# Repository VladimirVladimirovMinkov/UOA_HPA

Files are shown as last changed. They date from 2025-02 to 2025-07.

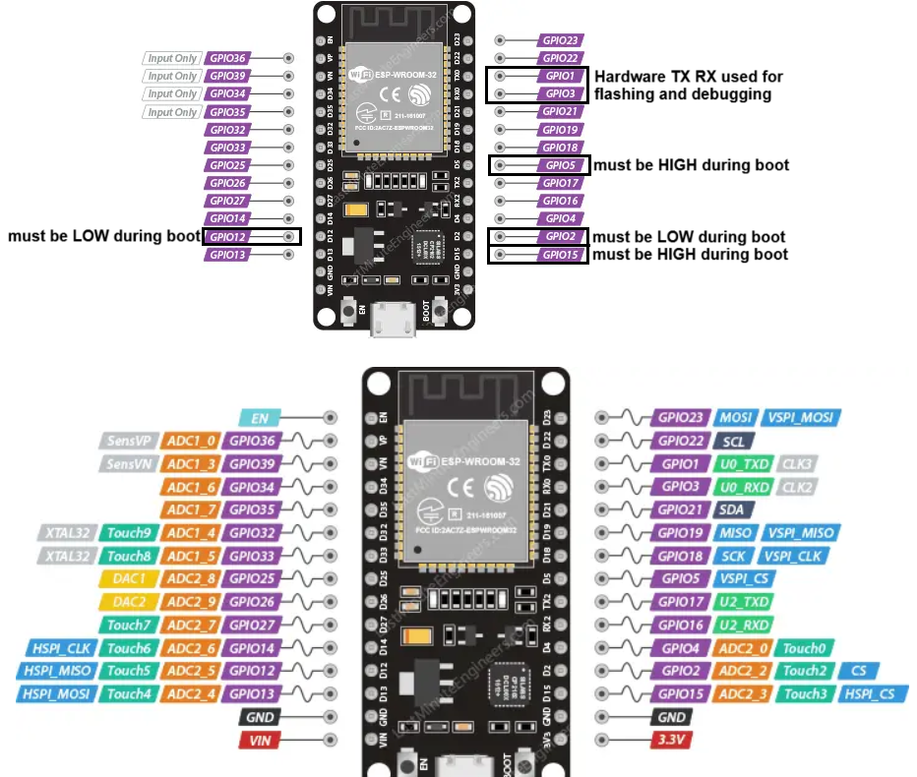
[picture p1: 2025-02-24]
src/ESP32 test code 1/esp32 wroom32 workable pins.png

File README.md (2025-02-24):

# UACHPA

This is a code and document repository for the University of auckland Aeronaughtics Club Human Powered Aircraft

# Overview

Repository Structure:
* Documents: This folder contains documents and reports made relating to the HPA
* CAD: Contains Computer Aided Design projects such as SOLIDWORKS or KiCAD
* src: This is for the code for the control systems and input mapping
* Test: This is the RnD folder for prototypes and demos that don't 100% work

# Getting involved
Please respect the repository structure and make sub folders if you're adding to the project so it is easier to navigate the repository

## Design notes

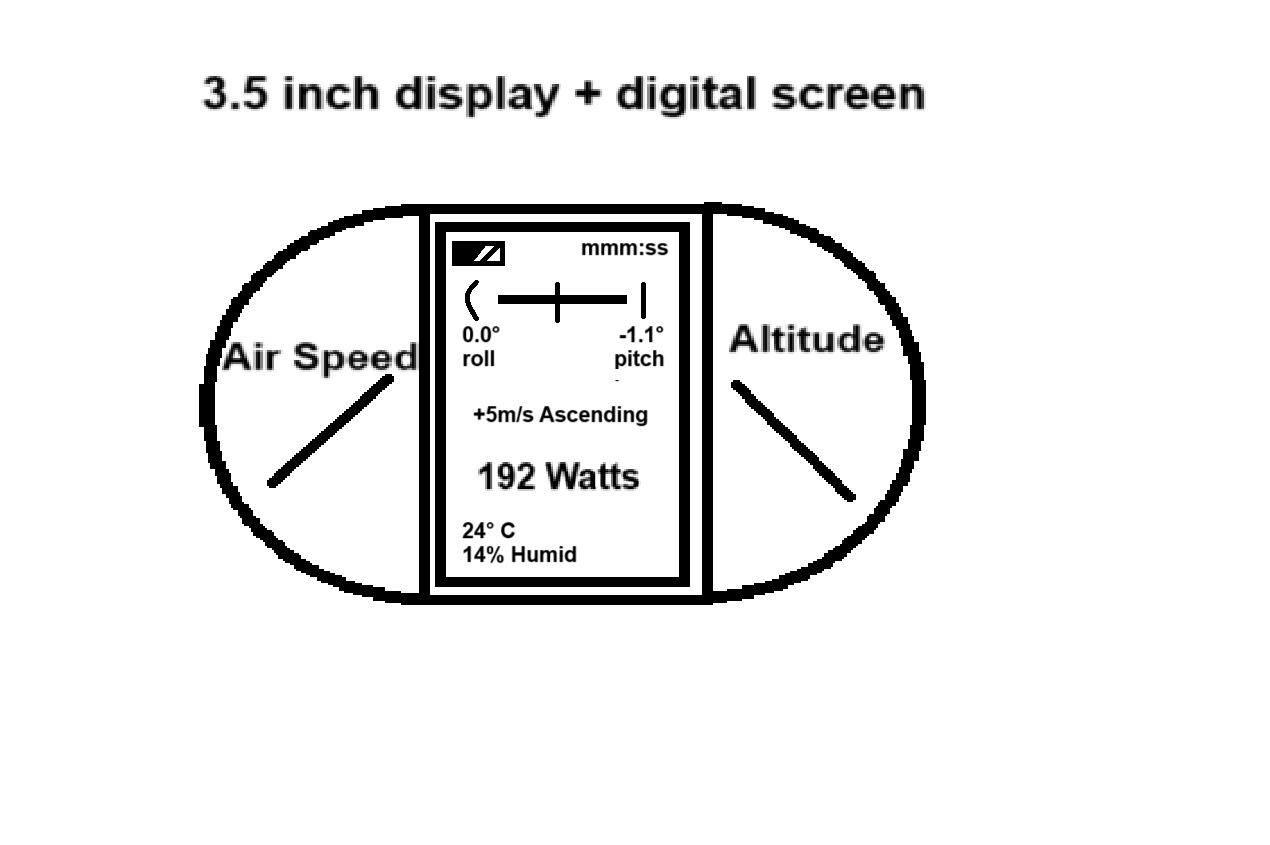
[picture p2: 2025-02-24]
Documents/Made/new display.png

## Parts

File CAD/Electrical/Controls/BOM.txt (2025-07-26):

'Value' 'Qty'
'4.7uf Capacitor' '4'
'10uf Capacitor' '5'
'Servo' '2'
'SD card reader' '1'
'BME280' '1' or BMP just don't get the connections confused
'potentiometer' '2'
'Battery 3.6V' '6' minimum we want 2
'Restart/Boot Button' '1'
'GPS' '1'
'Cadence Sensor Hall Effect' '4'
'Gyroscope' '1'
'LCD' '1'
'pitot tube assembly' '1'
'0ohm Jumper' '3' wire or 0ohm resistor or solder connection
'10k resistor' '4'
'1k resistor' '3'
'12k resistor' '1'
'23.3k resistor' '1'
'3.5k resistor' '1'
'5V regulator' '1'
'3V3 regulator' '1'
'3-6V to 6V DC/DC converter' '1'
'ESP32-WROOM-32E' '1'

'SD card Connector' '1' 1x6
'External Connector' '1' 1x4
'BME280 Connector' '1' 1x4
'Pitch Control Connector' '1' 1x3
'Roll Control Connector' '1' 1x3
'SD card selecting jumper' '1' 1x15
'SD card selecting connector' '1' 1x4
'Battery Connector' '1' 1x4 we can use a 1x2 if we don't use a charger and make our own battery pack
'GPS Connector' '1' 1x4
'Cadence Sensor Connector' '4' 1x3
'Gyroscope Connector' '1' 1x4
'pitot tube assembly Connector' '1' 1x3
'LCD connector' '1' 1x15 or break it up
'Elevator Servo Connector' '2' 1x3
'Rudder Servo Connector' '2' 1x3

6x
https://surplustronics.co.nz/products/1546-pcb-header-strip-single-in-line-40-pin

1x
https://epartners.co.nz/products/bme-280-spi-i2c-humidity-temperature-and-barometric-pressure-sensor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

4x
https://surplustronics.co.nz/products/1255-47-uf-50v

5x
https://surplustronics.co.nz/products/11991-10-uf-16v-

2x
https://hobbystation.co.nz/omg-20kg-stainless-steel-gear-servo-ip67-waterpoor-standard-size/

1x
https://surplustronics.co.nz/products/12112-sd-card-module-for-arduino

2x
https://surplustronics.co.nz/products/1684-1k-linear-potentiometer-

6x 
https://www.jaycar.co.nz/18650-rechargeable-li-ion-battery-2600mah-3-7v/p/SB2308

2x
https://surplustronics.co.nz/products/2157-switch-tact-push-button-momentary

1x
https://surplustronics.co.nz/products/7255-gps-module-for-arduino-with-antenna

4x
https://surplustronics.co.nz/products/2858-hall-effect-sensor-a3144-a3144e

1x
https://surplustronics.co.nz/products/6430-neo-rare-earth-magnet-ultra-small-100-pack

1x
https://surplustronics.co.nz/products/8352-9-axis-altitude-gyro-accelerator-magnetometer-sensor-module

1x - The smaller screen is good for testing but is too small for use
https://www.jaycar.co.nz/duinotech-arduino-compatible-2-5-inch-colour-lcd-touch-screen-display/p/XC4630

https://epartners.co.nz/products/st7008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

1x
https://epartners.co.nz/products/bme-280-spi-i2c-humidity-temperature-and-barometric-pressure-sensor
https://nz.element14.com/nxp/mpxv7002dp/sensor-pressure-dual-diff-0-02bar/dp/2080499
https://www.aliexpress.com/item/1005005646318954.html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!!!

1x
https://surplustronics.co.nz/products/1629-10k-ohm-resistor-pk-10

1x
https://surplustronics.co.nz/products/1605-1k-ohm-resistor-pk-10

1x
https://surplustronics.co.nz/products/1597-390-ohm-resistor-pk-10

1x
https://surplustronics.co.nz/products/1620-4k7-ohm-resistor-pk-10

1x
https://surplustronics.co.nz/products/1616-3k3-ohm-resistor-pk-10

1x
https://www.jaycar.co.nz/7805-5v-1a-voltage-regulator-to-220-case/p/ZV1505

1x
https://nz.mouser.com/ProductDetail/ROHM-Semiconductor/BA033T?qs=4kLU8WoGk0sYiXn4dS5I2A%3D%3D

1x
https://www.digikey.co.nz/en/products/detail/pololu/2892/10451203

1x
https://surplustronics.co.nz/products/11668-esp32-development-board-ch9102x

4x
https://www.aliexpress.com/item/1005008164500725.html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,scm-url:1007.40050.354490.0,pvid:906e5bc9-1d6b-4ea7-8844-5ef46c0b5282,tpp_buckets:668%232846%238112%231997&pdp_ext_f=%7B%22order%22%3A%223%22%2C%22eval%22%3A%221%22%2C%22sceneId%22%3A%2230050%22%7D&pdp_npi=4%40dis%21NZD%2119.33%2119.33%21%21%2181.76%2181.76%21%402101effb17461513513682025e7eb6%2112000044053778925%21rec%21NZ%21%21ABX&utparam-url=scene%3ApcDetailTopMoreOtherSeller%7Cquery_from%3A#nav-specification

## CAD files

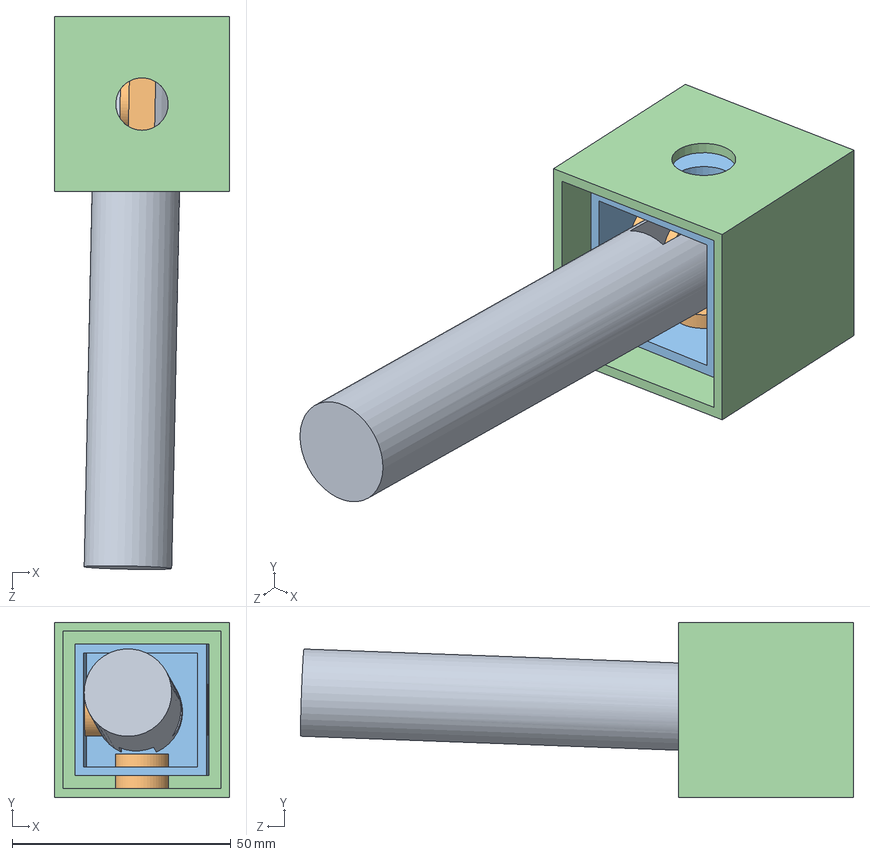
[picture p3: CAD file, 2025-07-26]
CAD/Mechanical/control stick/potentiometer/Assem1.SLDASM
40.0 x 40.1 x 126.3 mm
outer
inner
pin x 2
pole

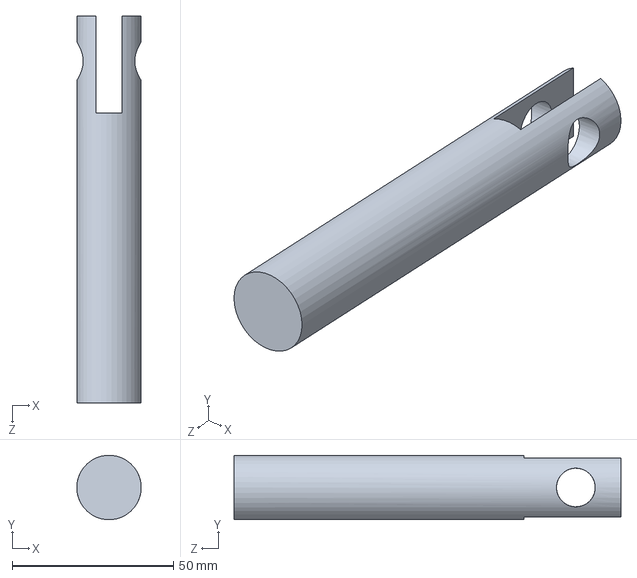
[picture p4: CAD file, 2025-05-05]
CAD/Mechanical/control stick/potentiometer/pole.SLDPRT
20.0 x 19.9 x 120.0 mm

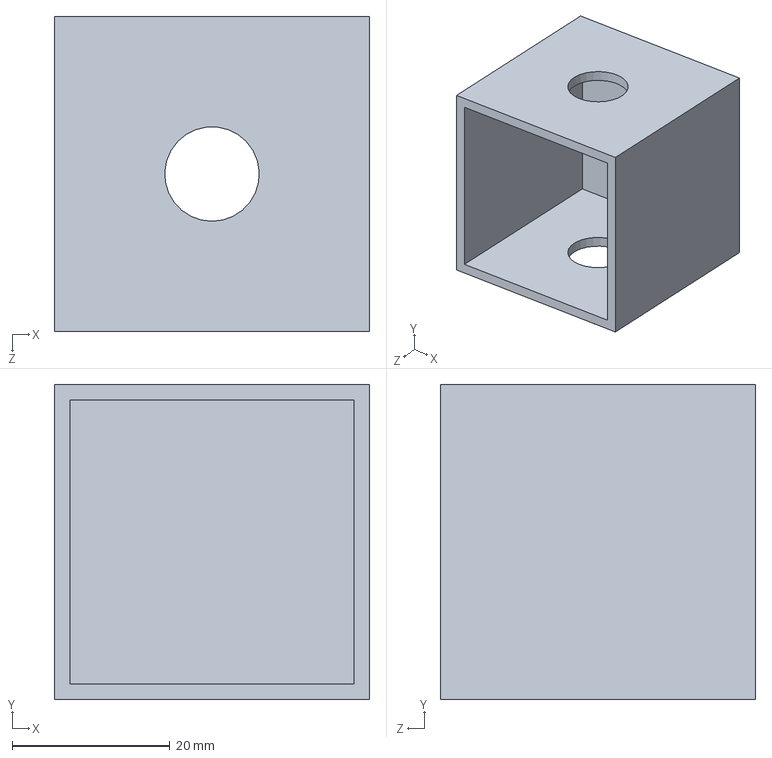
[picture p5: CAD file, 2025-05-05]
CAD/Mechanical/control stick/potentiometer/outer.SLDPRT
40.0 x 40.0 x 40.0 mm

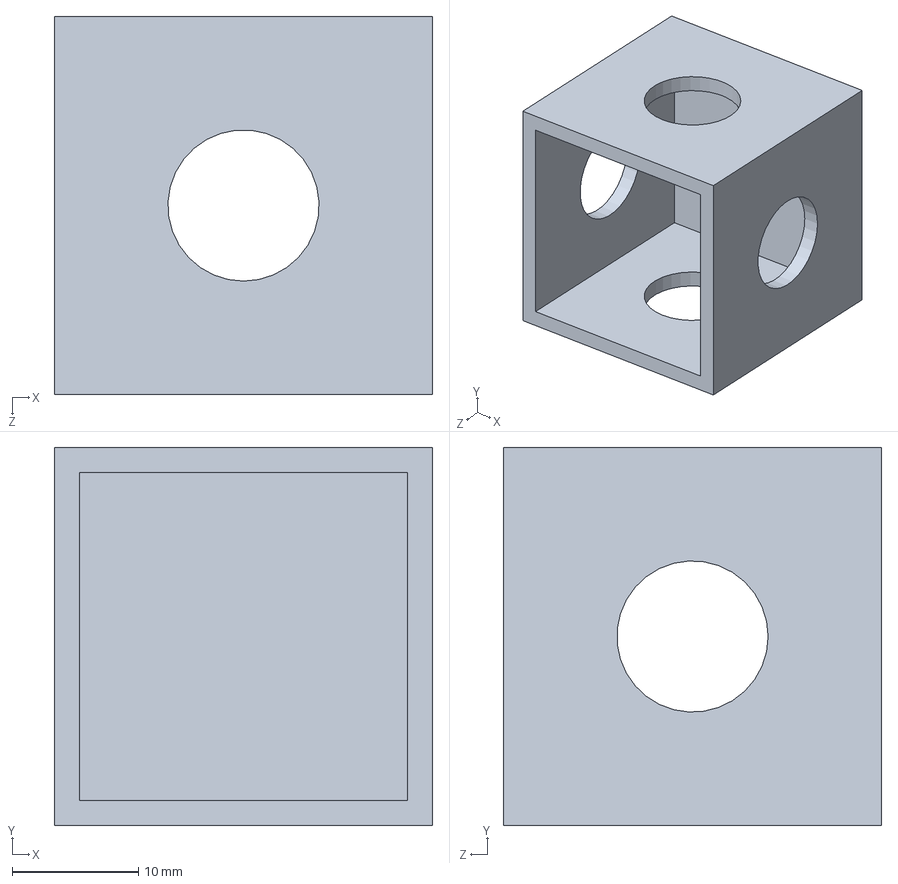
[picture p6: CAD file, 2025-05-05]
CAD/Mechanical/control stick/potentiometer/inner.SLDPRT
30.0 x 30.0 x 30.0 mm

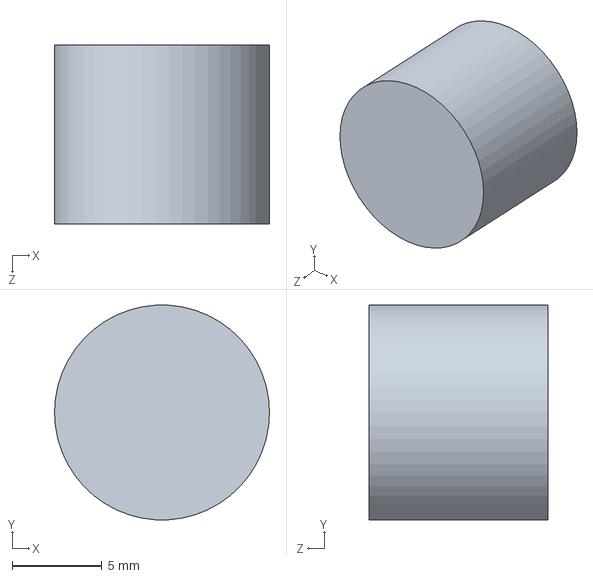
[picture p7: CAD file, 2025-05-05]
CAD/Mechanical/control stick/potentiometer/pin.SLDPRT
12.0 x 12.0 x 10.0 mm

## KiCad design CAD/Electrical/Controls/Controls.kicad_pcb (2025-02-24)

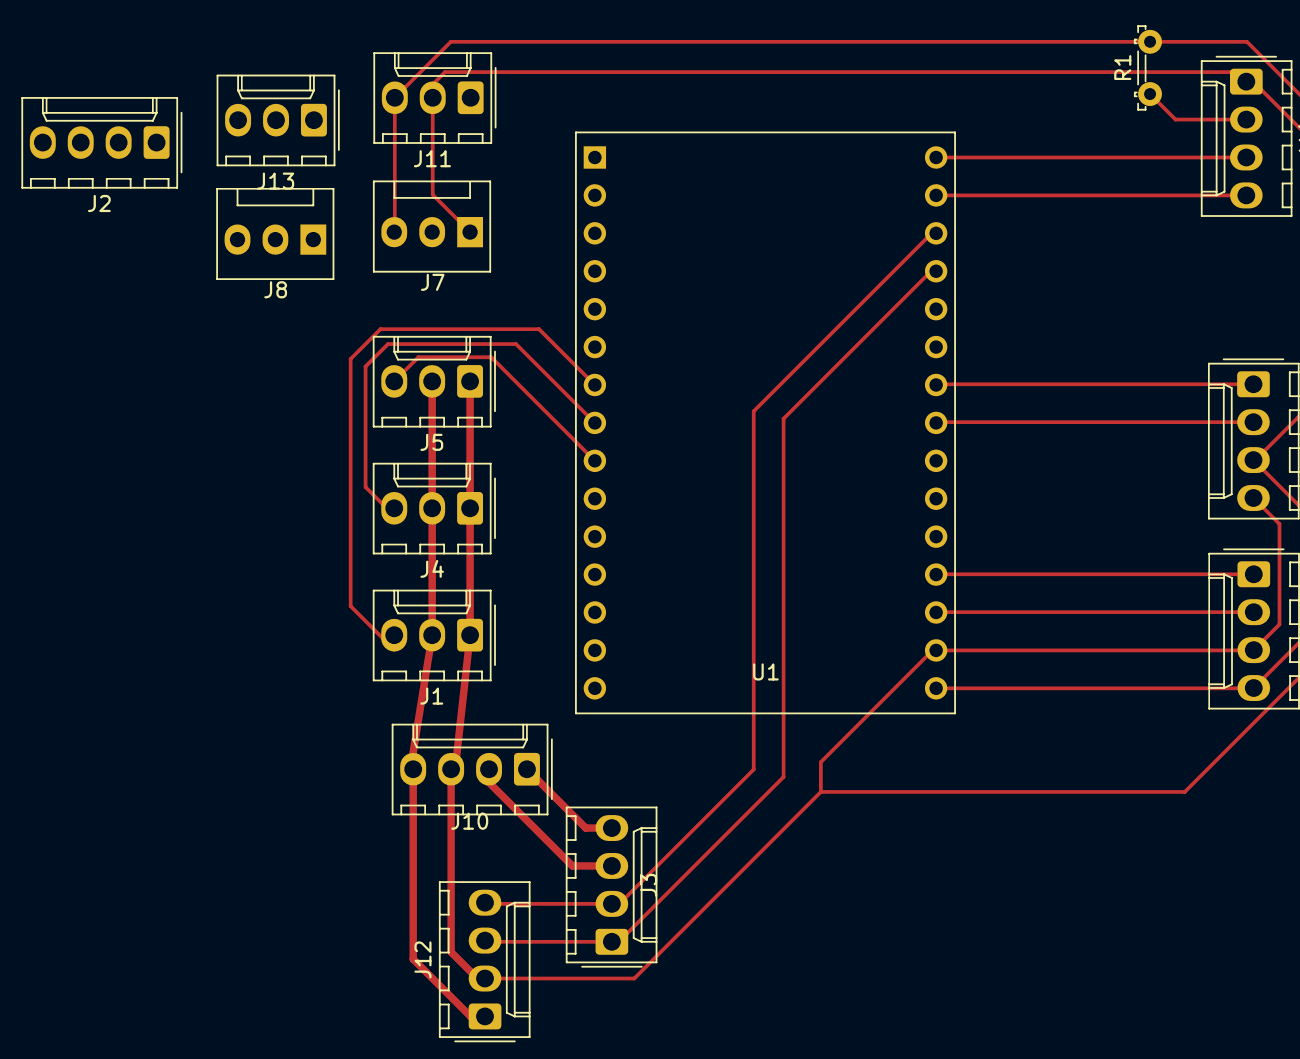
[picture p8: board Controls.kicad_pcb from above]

Board: 2 copper layers, 16 parts (0 on the bottom side), 22 nets.

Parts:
J1: Aileron Servo; Molex_KK-254_AE-6410-03A_1x03_P2.54mm_Vertical
J2: pitot tube assembly; Molex_KK-254_AE-6410-04A_1x04_P2.54mm_Vertical
J3: External Connector; Molex_KK-254_AE-6410-04A_1x04_P2.54mm_Vertical
J4: Rudder Servo; Molex_KK-254_AE-6410-03A_1x03_P2.54mm_Vertical
J5: Elevator Servo; Molex_KK-254_AE-6410-03A_1x03_P2.54mm_Vertical
J6: BME280; Molex_KK-254_AE-6410-04A_1x04_P2.54mm_Vertical
J7: Pitch Control; FanPinHeader_1x03_P2.54mm_Vertical
J8: Roll Control; FanPinHeader_1x03_P2.54mm_Vertical
J9: SD card; Molex_KK-254_AE-6410-04A_1x04_P2.54mm_Vertical
J10: Battery and/or BMS; Molex_KK-254_AE-6410-04A_1x04_P2.54mm_Vertical
J11: Restart/Boot Button; Molex_KK-254_AE-6410-03A_1x03_P2.54mm_Vertical
J12: GPS; Molex_KK-254_AE-6410-04A_1x04_P2.54mm_Vertical
J13: Cadence Sensor; Molex_KK-254_AE-6410-03A_1x03_P2.54mm_Vertical
J14: Gyroscope; Molex_KK-254_AE-6410-04A_1x04_P2.54mm_Vertical
R1: Jumper; R_LDR_5.2x5.2mm_P3.5mm_Horizontal
U1: ESP32-C3-DevKitM-1

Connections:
unnamed: J1.1, J2.2, J4.1, J5.1, J6.3, J7.3, J8.3, J9.4, J10.3, J11.3, J12.2, J13.1, J14.2, R1.1, R1.2, U1.14 (GND), U1.17 (GND)
unnamed: J1.2, J4.2, J5.2, J10.4, J12.1, U1.15 (VIN)
unnamed: J1.3, U1.7 (D33)
unnamed: J2.3, U1.6 (D32)
unnamed: J2.4, U1.3 (VN)
unnamed: J4.3, U1.8 (D25)
unnamed: J5.3, U1.9 (D26)
unnamed: J6.1, U1.19 (D2)
unnamed: J6.2, U1.18 (D15)
unnamed: J7.2, U1.4 (D34)
unnamed: J8.2, U1.5 (D35)
unnamed: J9.1, U1.24 (D18)
unnamed: J9.2, U1.23 (D5)
unnamed: J3.4, J10.1
unnamed: J3.3, J10.2
unnamed: J11.1, U1.1 (EN)
unnamed: J2.1, J6.4, J7.1, J8.1, J9.3, J11.2, J13.2, J14.1, U1.16 (3.3V)
unnamed: J3.1, J12.3, U1.27 (RX0)
unnamed: J3.2, J12.4, U1.28 (TX0)
unnamed: J13.3, U1.2 (VP)
unnamed: J14.3, U1.30 (D23)
unnamed: J14.4, U1.29 (D22)

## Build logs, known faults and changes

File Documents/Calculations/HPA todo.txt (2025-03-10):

High Priority:
Select an Airspeed indicator - pitot tube assembly
https://nz.element14.com/nxp/mpxv7002dp/sensor-pressure-dual-diff-0-02bar/dp/2080499
https://www.aliexpress.com/item/1005005646318954.html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!!!
2 pins

Select a Cadence measuring system (sensors) - 
https://surplustronics.co.nz/products/2858-hall-effect-sensor-a3144-a3144e
1 rotation = 2 steps
needs magnet(s)
1 pin

Select servos (could use the same ones used last time) - use the same ones as last time or buy https://www.rcinnovations.co.nz/servos/4229-ecopower-wp110t-cored-waterproof-high-torque-metal-gear-digital-servo-.html
1x3 = 3 pins

each servo needs up to 1.5A at 5V
https://www.aliexpress.com/item/1005003380492497.html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

https://surplustronics.co.nz/products/1741-lm7805-1-amp-ve-5v

Write up short report doing some math justifying the torque on these motors -
Math from before and the EASA microlight specs and the servo selection table math and safety factor of at least 1.5x

Select a lightweight but big display for real time updates - servo mounted on screen or 
https://surplustronics.co.nz/products/10716-blue-oled-lcd-display-module-128x64-096-inch-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
2 pins
if that's too small or if a couple together can't fit on a board
https://www.jaycar.co.nz/duinotech-arduino-compatible-2-5-inch-colour-lcd-touch-screen-display/p/XC4630
6 pins for display only 2 pins for SD card

https://forum.arduino.cc/t/reading-data-from-a-sensor-over-i2c-interupts-my-display-output/1081907/6

tutorial

big but not light weight 7' we don't need something bigger then this period. (unless it's for the ground station)
https://www.aliexpress.com/item/1005006471099177.html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,scm-url:1007.40050.354490.0,pvid:f4fbe6a5-cb32-471b-ba21-d99bef410eae,tpp_buckets:668%232846%238114%231999&pdp_npi=4%40dis%21NZD%2174.43%2140.93%21%21%21300.62%21165.34%21%402103209b17387310687954766e41cb%2112000037319951906%21rec%21NZ%21%21ABX&utparam-url=scene%3ApcDetailTopMoreOtherSeller%7Cquery_from%3A

Select a joystick (requirements is mostly easy for pilot to use and provides some resistance/ ie not too sensitive)
Piston(maybe constant force) with a lever on an axel

	side on	<-\->  pitch   		  head on  <-|-> yaw
lever on axel 	 --D           			axel o <- this spins

using a tilt sensor for both pitch and yaw 1 pin each for 2 pins

Choose an SD card reader (figure out how much data is actually expected to be stored on it per flight)
https://surplustronics.co.nz/products/12112-sd-card-module-for-arduino if needed
with a 2GB SD card and 1 update of full screen pixel and color depth per second is worth just under half an hour
2 pins

Figuring out our requirements are important as this would indicate what type of chip we need and how components will interface with the chip and each other

total 16 pins
Battery level and instrumentation checking can be done separately from control systems but it would need 1 pin each 
totaling to 18 pins or 16 if the battery level and instrumentation checks are done by the diagnostic instrumentation/kit
Arduino is small and slow but workable for our purposes(at least for now)
esp32-wroom-32 has 23 usable GPIO pins (says more but some are boot pins that cause problems when used or for 1 use)
STM needs Mbed or Em bed but similar to Arduino 
NRF best for our use case but not user friendly 
Regardless of what chip we use, we will need a small heat radiator/sink 

Mid Priority:
Pick a chip that we could all use
Create a data budget for everything getting stored on the SD card (might be overkill if flight isn't very long)
Pick a battery for supply -> lil voltage regulator
Figure out what is needed for the linkage system / the actual control surfaces
should figure out range of motion on these and have some system that doesn't let them exceed these limits
Design a diagnostic check display that is modular and can be removed preflight -> diagnostic instruments/kit
checks battery levels, servo function, joystick control and all other instruments -> diagnostic instruments/kit

the diagnostic instruments/kit is an added device to the connector port that connects to the calibration/test systems and the control systems to check all equipment is functioning and checks battery levels

Low Priority :
Eventually for PCB need to select the following, best to have an idea of what the requirements for each are
GPS -> just get a GPS from surplustronics and log to SD card -> not the same as Altimeter
Altimeter + an external IR or similar sensor to validate take-off time -> 2nd pitot tube + strain sensor on wheel 
external ADC for noise reduction or capacitors / lowpass filter type shenanigans -> yes also inductors and multi sampling
Molex / RJ45 / whatever connector we wanna use (i can steal these from work for free so good to know which is best)
Molex for battery charging, RJ45 is harder and no charging, m12 is optimal but can be replaced by a Molex with a Bung
We need 4 pins minimum up to 8 for the connector

Considerations for later:
Using Bluetooth/RF stuff
Using buttons for control
Mounting for all these systems
Pilot interface
Control surfaces
Servos and battery
Harnessing

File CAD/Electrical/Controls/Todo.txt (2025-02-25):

Now:
1. Change Devkit to ESP32 WROOM chip (GPIO pins don't need to be changed, just transferred over for the different pin layout)
2. Decide on the servo (the previously recommended servo is no longer in production or sale)
3. Voltage regulators 
	6V to 4V for each servo
	3.3V esp32, I2C devices, SPI devices and controls
	5V for pitot tube

4. Draw up PCB
5. Review

Later:
1. Print PCB
2. Solder
3. Code
4. Test

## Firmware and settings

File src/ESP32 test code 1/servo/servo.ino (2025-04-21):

void setup() {
  Serial.begin(115200);

  pinMode(14, INPUT);
  pinMode(27, INPUT);
  pinMode(12, OUTPUT);
  pinMode(13, OUTPUT);
  delay(100);
  digitalWrite(12, LOW);
  digitalWrite(13, LOW);
  delay(100);
}

long start;
int rudder = 1000;
int elevator = 1000;
int events[12];

void loop() {
  while(Serial.available()>0)
  {
    if(Serial.peek() == 's')
    {
      rudder = 1000;
      elevator = 1000;
      delay(1000);
    }
    Serial.write(Serial.read());
  }


  start = micros();
  digitalWrite(13, HIGH);
  while (micros() - start < rudder);
  digitalWrite(13, LOW);

  start = micros();
  digitalWrite(12, HIGH);
  while (micros() - start < elevator);
  digitalWrite(12, LOW);

  for(int i = 0; i < 5; i++)
  {
    start = micros();
    rudder = (analogRead(14)/3)+500;
    elevator = (analogRead(27)/3)+500;

    events[i*2] =  rudder;
    events[i*2+1] = elevator;
    // 10 milisconds of code

    while (micros() - start < 10000);
  }
  events[10] = random(200); // heart rate
  events[11] = micros();
  // save the events to eeprom or sd
}

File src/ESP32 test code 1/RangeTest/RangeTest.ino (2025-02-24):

void setup() {
  pinMode(16, OUTPUT);
  digitalWrite(16, LOW);
  delay(100);
}

void loop() {
  for(int i = 60; i < 76; i+=3)
  {
    for(int j = 26; j > 0; j-=8)
    {
      digitalWrite(16, LOW);
      delay((i-j)/4);
      digitalWrite(16, HIGH);
      delay((i-j)/4);

      digitalWrite(16, LOW);
      delay((i-j)/4);
      digitalWrite(16, HIGH);
      delay((i-j)/4);

      digitalWrite(16, LOW);
      delay((i-j)/4);
      digitalWrite(16, HIGH);
      delay((i-j)/4);
    }
  }
}

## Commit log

2025-02-24 Initialize repo
    [Controls.kicad_pcb, Controls.kicad_sch]
2025-02-25 Added more electrical components
    [Controls.kicad_sch]
2025-02-25 Schematic update
2025-02-25 Mostly done schematic
    the voltage regulators are done
    need to rewire from dev board to esp32
    then PCB drawing
    [Controls.kicad_sch]
2025-02-25 BOM
    bill of materials
    there's an export function in KiCAD
    use python to split by " to get name and number used
2025-03-04 Schematic and almost BOM
    [Controls.kicad_sch]
2025-03-10 schematics and weight update
    [Controls.kicad_sch]
2025-03-20 update
    soon to break up the schematic
    [Controls.kicad_sch]
2025-05-05 hole in rod
    [Assem1.SLDASM, inner.SLDPRT, outer.SLDPRT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]
2025-07-26 Rejig and modify BOM
    [Assem1.SLDASM]
